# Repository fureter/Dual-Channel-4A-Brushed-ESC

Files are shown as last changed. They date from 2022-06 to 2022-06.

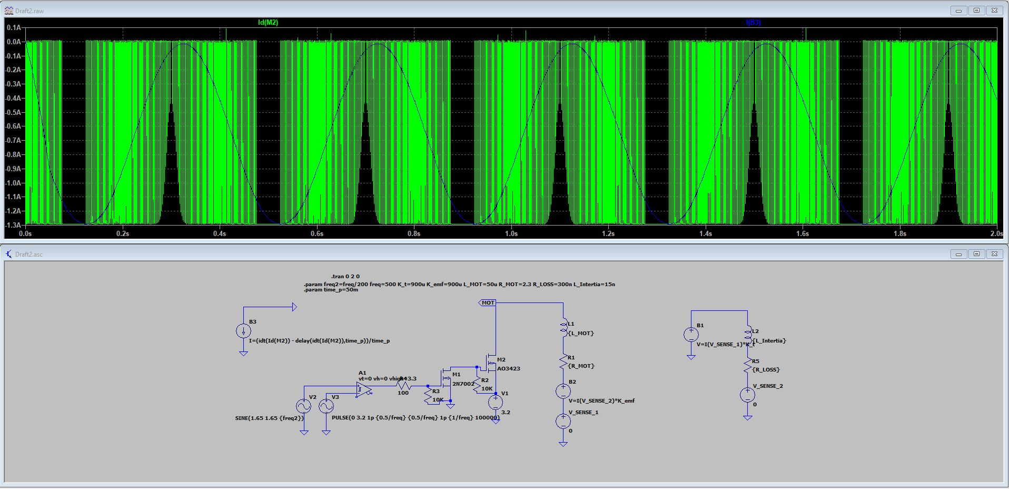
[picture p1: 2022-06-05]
sim/LTSpice_Sim.JPG

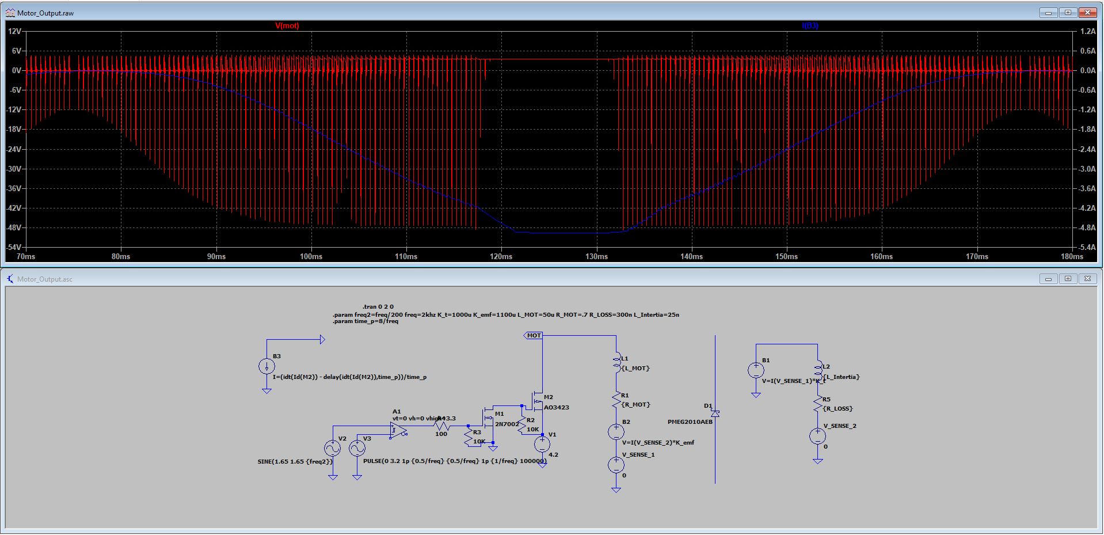
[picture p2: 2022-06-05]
sim/no_flyback_diode.JPG

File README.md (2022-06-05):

# Dual Channel 4A 1S Brushed ESC
 
### Features:
- Two motor control channels
- Two PWM inputs (Throttle and Mix)
- Customizable motor mixing
- 2A 5V BEC to power external electronics (FPV, receiver, etc)
- 4A motor driver
- Customizable ESC settings using throttle input on startup
- Two LEDs for status while changing settings
- Low battery detection
- Customizable low voltage cutoff
- Small form factor 13.5x25.6mm
- Low weight 3.26g (with external cap and connectors)

### Software:
Software for the ESC is written in C for STM8S using SDCC for compilation. Included in the software directory is a makefile for compiling the software.

### Hardware:
Hardware was designed using KiCad and all applicable files are included in the hardware directory. Also included in the hardware directory are the files required for manufacturing from JLCPCB. Manual assembly is required for the bottom side of the board and the connectors.

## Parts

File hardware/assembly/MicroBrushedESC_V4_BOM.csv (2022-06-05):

Designator | Quantity | Comment | Footprint | LCSC Part #
C1 C5 | 2 | 1uF | Capacitor_SMD:C_0402_1005Metric | C52923
C2 C6 C8 C9 | 4 | 22u | Capacitor_SMD:C_0603_1608Metric | C59461
C3 | 1 | 10n | Capacitor_SMD:C_0402_1005Metric | C272878
C4 | 1 | 100nF | Capacitor_SMD:C_0402_1005Metric | C1525
C7 | 1 | 100uF | Capacitor_Tantalum_SMD:CP_EIA-3528-21_Kemet-B | C16133
D1 | 1 | LED_Small | LED_SMD:LED_0603_1608Metric | C2286
D4 | 1 | LED_Small | LED_SMD:LED_0603_1608Metric | C72041
D2 D3 | 2 | D_Schottky | Diode_SMD:D_SOD-123 | C8598
J1 | 1 | MOTOR1 | Connector_Molex:Molex_PicoBlade_53047-0210_1x02_P1.25mm_Vertical
J2 | 1 | MOTOR2 | Connector_Molex:Molex_PicoBlade_53047-0210_1x02_P1.25mm_Vertical
J3 | 1 | CONTROL | Connector_Molex:Molex_PicoBlade_53047-0410_1x04_P1.25mm_Vertical
J4 | 1 | VBAT+ | Connector_PinHeader_1.27mm:PinHeader_1x01_P1.27mm_Vertical
J5 | 1 | REPROG | Connector_Molex:Molex_PicoBlade_53047-0410_1x04_P1.25mm_Vertical
J6 | 1 | VBAT- | Connector_PinHeader_1.27mm:PinHeader_1x01_P1.27mm_Vertical
L1 | 1 | 1u | Inductor_SMD:L_Vishay_IHLP-1616 | C135266
Q1 Q2 | 2 | 2N7002 | Package_TO_SOT_SMD:SOT-23 | C8545
Q3 Q4 | 2 | AO3401A | Package_TO_SOT_SMD:SOT-23 | C15127
R1 R12 | 2 | 5k | Resistor_SMD:R_0402_1005Metric | C166638
R13 | 1 | 402k | Resistor_SMD:R_0402_1005Metric | C11586
R2 R3 | 2 | 100 | Resistor_SMD:R_0402_1005Metric | C25076
R4 R5 R6 R7 | 4 | 10k | Resistor_SMD:R_0402_1005Metric | C25744
R8 R10 R11 R14 | 4 | 100k | Resistor_SMD:R_0402_1005Metric | C106234
R9 | 1 | 1M | Resistor_SMD:R_0402_1005Metric | C269676
U1 | 1 | STM8S003F3P | Package_SO:TSSOP-20_4.4x6.5mm_P0.65mm | C52717
U2 | 1 | TPS61230 | digikey-footprints:VSON-10-1EP_3x3mm | C139626

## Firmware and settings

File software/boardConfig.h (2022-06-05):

/*
 *	File used to define channel mapping and board level mapping
 *
 */
#ifndef BOARDCONFIG_H
#define BOARDCONFIG_H
 
#include <stdint.h>
#include "stm8s.h"

#define BLUE_LED					((uint8_t)0x10)
#define LED_GPIO					GPIOB

#define GREEN_LED					((uint8_t)0x10)
#define LED_GREEN_GPIO				GPIOD

#define CH1_PIN 					((uint8_t)0x40)
#define CH2_PIN						((uint8_t)0x80)

#define DEFAULT_MIX					((uint8_t) 30)
#define DEFAULT_MIX_DIR				((uint8_t) 0)
#define DEFAULT_LVCO				((uint8_t) 0)
#define DEFAULT_FREQ_H				((uint8_t) (1599 >> 8))
#define DEFAULT_FREQ_L				((uint8_t) (1599 & 0xFF))
#define DEFAULT_DEADBAND			((uint8_t) 8)

#endif /* BOARDCONFIG_H */

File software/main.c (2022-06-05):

#define STM8S003 (1)
#include "boardConfig.h"
#include "stm8s.h"
#include "IOManager/delay.h"
#include "InitManager/init.h"
#include "IOManager/pwm.h"
#include "IOManager/battery.h"


int main(){
	init();
	while(1){
		measure_input();
		mix_channels();
		write_motors();
		read_battery_voltage();
		if(is_lvco()){
		    LED_GREEN_GPIO->ODR = 0x00;
		}
		else{
		    LED_GREEN_GPIO->ODR = GREEN_LED;
		}
	}
	return 1;
}
